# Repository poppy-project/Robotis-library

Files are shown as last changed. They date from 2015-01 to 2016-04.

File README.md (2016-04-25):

Robotis CAD library
===================

Solidworks library of Robotis CAD models.
It includes the Dynamixel AX-Series and MX/RX-series.

In addition, there are 3D printable parts allowing for compact double rotation assemblies (available for 3 configuration (MX64-MX64, MX64-MX28, MX28-MX28))
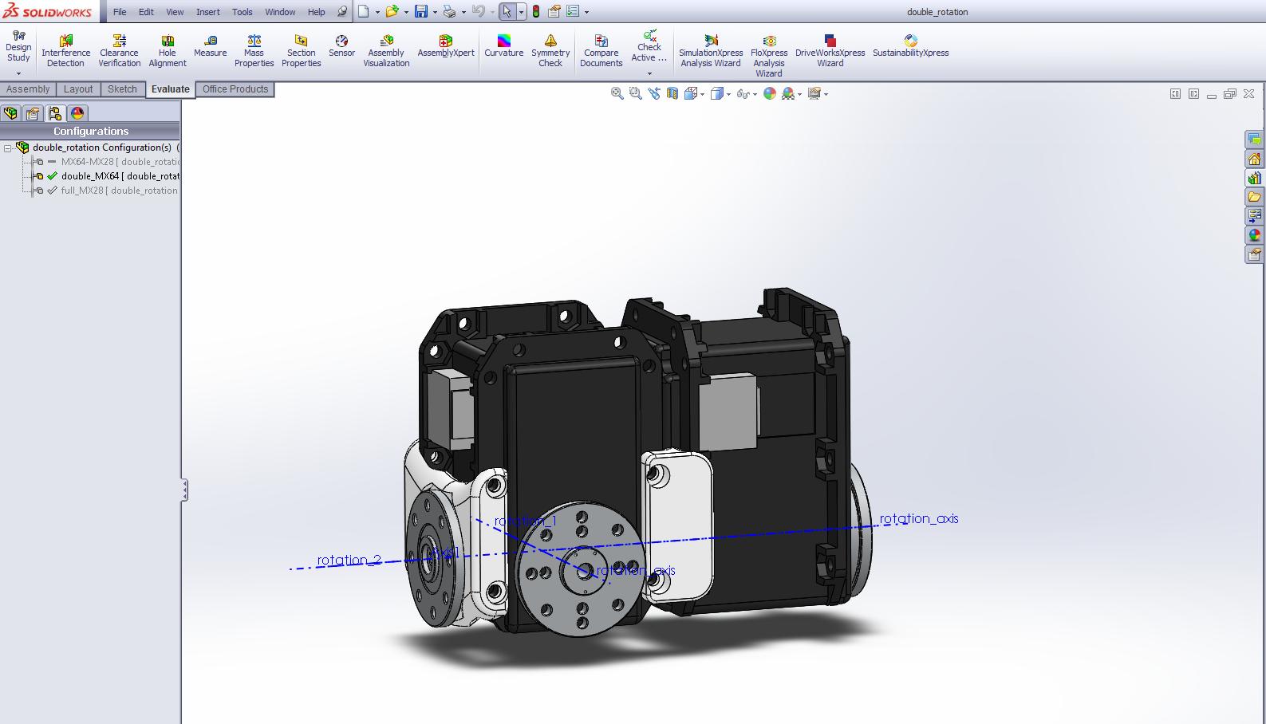
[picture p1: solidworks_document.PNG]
double-rotation


 **This work is licensed under a [Creative Commons Attribution-ShareAlike 4.0 International License](http://creativecommons.org/licenses/by-sa/4.0/).**

Please keep references to the Poppy project (www.poppy-project.org) and authors when you use or fork this work.

**Authors:** Matthieu Lapeyre, Alexandre Le Falher.

## Support

You need support ?
The [Poppy forum](https://forum.poppy-project.org/) is the best (and single) place to ask for help!

## Contribute

### /!\ SolidWorks version
The SolidWorks policy sucks, they intentionnaly break compatibility between recent and older version. If you have a Solidworks older than 2013-SP0 you will certainly be able to open these parts but only as a read-only mode, which is equivalent to not beign able to open it...

Therefore, we won't upgrade our SolidWorks so more people can easily modify parts for their own uses.

For the same reason, we ask potential contributors wanting to pull work into official repository to downgrade (if needed) their solidworks version to 2013.

Accepting a pull-request from a Soldiworks >= 2014 will break whole compatibility.

## The Poppy project history

The Poppy project is born in 2012 in the [Flowers laboratory](flowers.inria.fr) at [Inria Bordeaux Sud-Ouest](http://www.inria.fr/en/centre/bordeaux).
It was initiated during [Matthieu Lapeyre](github.com/matthieu-lapeyre)'s PhD Thesis surpervised by [Pierre Yves Oudeyer](http://www.pyoudeyer.com/). At the beginning, the development team was composed by Matthieu Lapeyre (mechanics & design), [Pierre Rouanet](github.com/pierre-rouanet) (software) and [Jonathan Grizou](http://jgrizou.com/) (electronics).

This project is initially a fundamental research project financed by [ERC Grant Explorer](http://erc.europa.eu/) to explore the role of embodiement and morphology properties on cognition and especially on the learning of sensori-motor tasks.

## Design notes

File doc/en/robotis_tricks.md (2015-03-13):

# /!\ Robotis Dynamixel Noobs Traps

When you want to assemble a Poppy, the first thing to do is to ensure yourself **you assembled correctly the horn on the Dynamixel motors**. This is both the first step and maybe the most critical one. An error in the configuration or assembly here is really boring to change once a Poppy creature is assembled.

## 1. Fix the horn on the motor
**Warning! This step is critical!**

Dynamixel motors are sold unassembled, you have to add manually the horn HN07-N101 (for MX-28) and HN05-N102 (for MX-64).
The critical aspect is to put the horn correctly on the zero position. To do that, you have to correctly align the awl mark on the Dynamixel shaft and the snick on the horn:

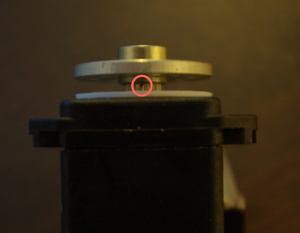
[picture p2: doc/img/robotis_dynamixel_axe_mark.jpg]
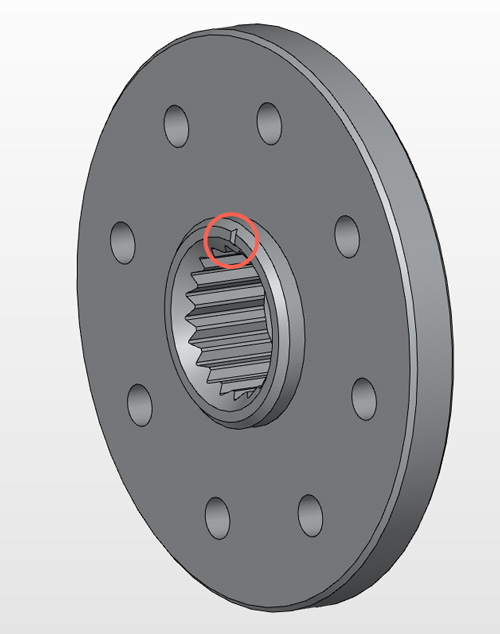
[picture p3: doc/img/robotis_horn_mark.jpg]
 

When assembled, the horn is really difficult to remove and you will probably damage the motor, so check twice or thrice !

Also, it is pretty hard to push the horn on the shaft, you will probably have to use the screw (M2.5x8mm) and tighten it to correctly assemble the two elements.

## 2. Motor configuration
When you take out the motor out of its box, its internal id is 1. So before plug it on the communication bus you have to configure it. Otherwise you will have problems such as experimented in this [topic](https://forum.poppy-project.org/t/dynamixel-first-uses/91/5).

You have 3 parameters to tune:

 1. the **id must match our [convention][1]**
 2. the **baudrate** have to be **set to 1 000 000bps** instead of 57142bps
 3. the **return delay time** have to be set to **0 ms** instead of 0.5 ms

To tune these parameters you can either use the [Dynamixel Wizard][2] (windows) or [Herborist][3] (Unix/Windows).
<a class="attachment" href="http://www.robotis.com/xe/download_en/657775">RoboPlus v1.1.1.0 </a>

If you are using [USB2AX dongles][4] under windows, you will need to install it manually using the <a class="attachment" href="https://github.com/Xevel/usb2ax/raw/master/firmware/lufa_usb2ax/USB2AX.inf">USB2AX.inf</a> (2 KB) file.
For more info about the installation procedure, please consult the [QuickStart guide][5].

  [1]: https://forum.poppy-project.org/t/assembly-instructions-motor-naming-convention-and-configuration/87
  [2]: http://support.robotis.com/en/software/roboplus/dynamixel_monitor/quickstart/dynamixel_monitor_connection.htm
  [3]: http://poppy-project.github.io/pypot/herborist.html
  [4]: http://www.xevelabs.com/doku.php?id=product:usb2ax:usb2ax
  [5]: http://www.xevelabs.com/doku.php?id=product:usb2ax:quickstart

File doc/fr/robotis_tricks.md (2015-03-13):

# /!\ Robotis Dynamixel : piège pour les débutants

Lorsque vous souhaitez assembler un Poppy, la première chose dont il faut vous assurer **est que vous assemblez correctement le palonnier des moteurs Dynamixel**. C'est à la fois la première étape et peut-être la plus critique. Une erreur dans la configuration ou l'assemblage de cette étape sera véritablement difficle à changer une fois que Poppy sera assemblé.

## 1. Gérer le palonnier sur le moteur
**ATTENTION ! Cette étape est critique !**

Les moteurs Dynamixel sont vendu non assemblés, vous aurez à ajouter manuellement le palonnier HN07-N101 (pour le modèle MX-28) et HN05-N102 (pour le modèle MX-64).
Le point critique est de placer le palonnier correctement, sur la position zéro. Pour le faire, vous aurez à aligner correctement la marque de poinçon de l'arbre avec l'entaille de le palonnier :

 

Quand montée, le palonnier est véritablement difficile à enlever et vous aurez certainement à endommager le moteur aussi, tourner sept fois vos doigts dans vos mains avant d'agir !

De même, il est assez difficile de placer le palonnier dans l'arbre, vous aurez certainement à utiliser une vis (M2.5x8mm) et la serrer pour assembler correctement les deux éléments.

## 2. Configuration des moteurs
Lorsque vous sortez le moteur de sa boîte, son ID interne est 1. Aussi, avant de le brancher sur le bus de communication, vous aurez à le configurer. Autrement vous aurez des problèmes comme expérimentés dans ce  [topic](https://forum.poppy-project.org/t/dynamixel-first-uses/91/5).

VOus avez trois paramètres à régler :

 1. L'**ID doit correspondre à notre [convention][1]**
 2. La **vitesse de transmission** doit être **réglée sur 1 000 000bps** au lieu de 57142bps
 3. Le  **délai de temps de retour** doit être réglé sur **0 ms** au lieu de 0.5 ms

Pour régler ces paramètres vous pouvez utiliser le [Dynamixel Wizard][2] (windows) ou [Herborist][3] (Unix/Windows).
<a class="attachment" href="http://www.robotis.com/xe/download_en/657775">RoboPlus v1.1.1.0 </a>

Si vous utilisez [une prise USB2AX][4] sous windows, vous aurez à l'installer manuellement en utilisant ce fichier : <a class="attachment" href="https://github.com/Xevel/usb2ax/raw/master/firmware/lufa_usb2ax/USB2AX.inf">USB2AX.inf</a> (2 KB).
Pour plus d'infos sur cette installation, merci de consulter le [guide d'installation][5].

  [1]: https://forum.poppy-project.org/t/assembly-instructions-motor-naming-convention-and-configuration/87
  [2]: http://support.robotis.com/en/software/roboplus/dynamixel_monitor/quickstart/dynamixel_monitor_connection.htm
  [3]: http://poppy-project.github.io/pypot/herborist.html
  [4]: http://www.xevelabs.com/doku.php?id=product:usb2ax:usb2ax
  [5]: http://www.xevelabs.com/doku.php?id=product:usb2ax:quickstart

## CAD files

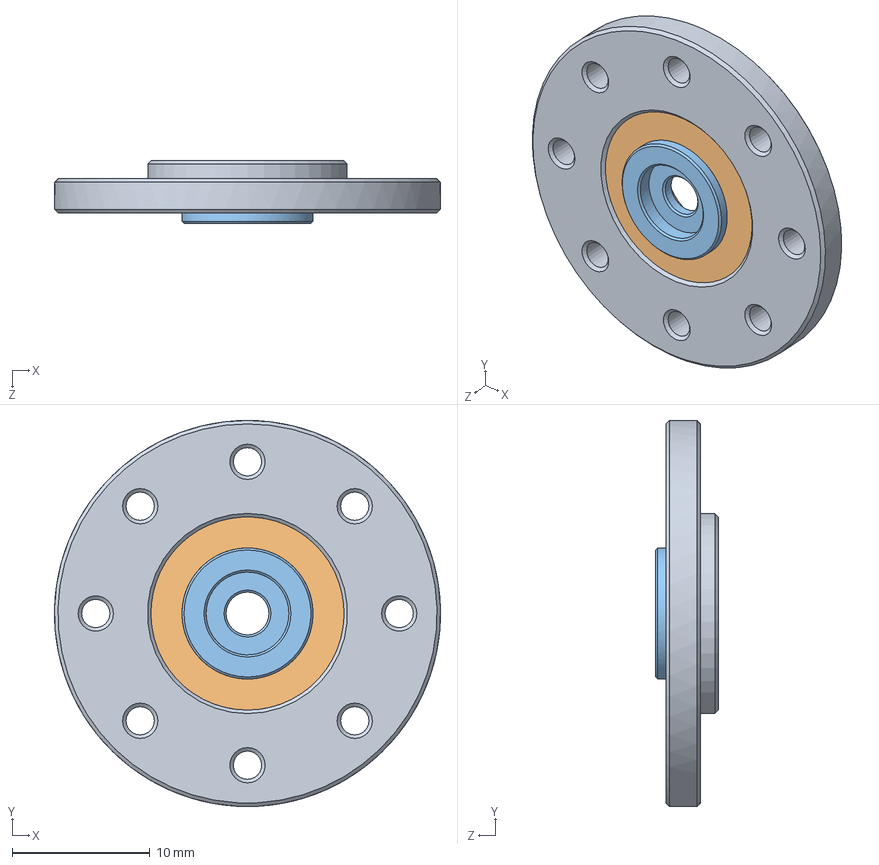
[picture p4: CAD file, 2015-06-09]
bearing/i101_Set.SLDASM
28.0 x 28.0 x 4.56 mm
HN05-i101
MF128ZZ
RX64-CAP

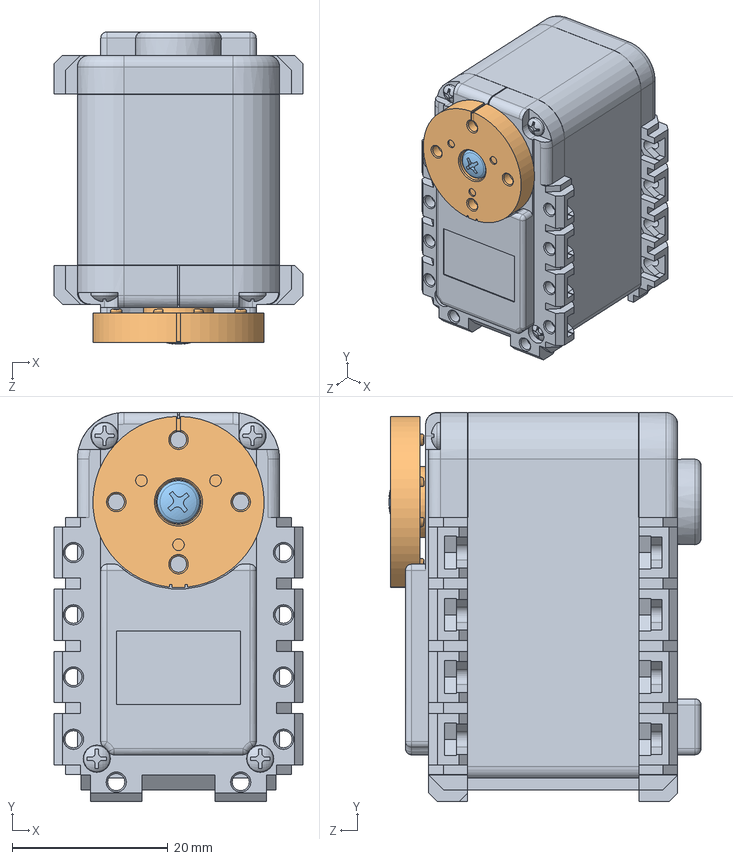
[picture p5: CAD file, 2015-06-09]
AX-12_18A.SLDASM
32.0 x 50.0 x 40.1 mm
dynamixel_AXseries
AX12_horn
BHS_M2_6X8

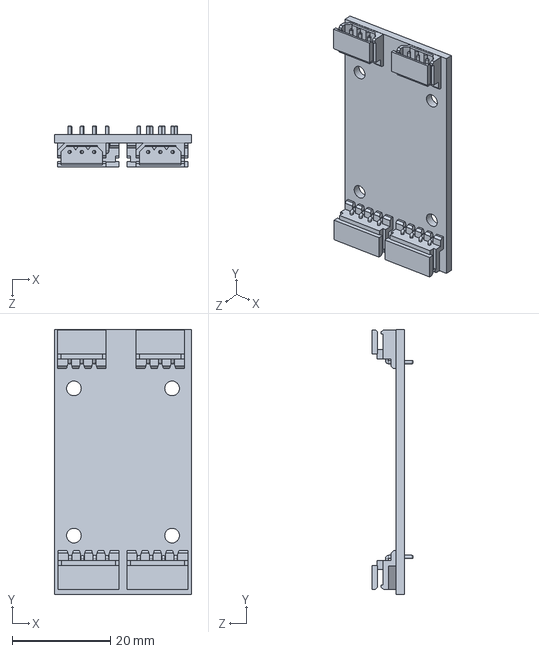
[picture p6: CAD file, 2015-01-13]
electronics/SMPS2Dynamixel.SLDPRT
28.0 x 54.0 x 8.40 mm

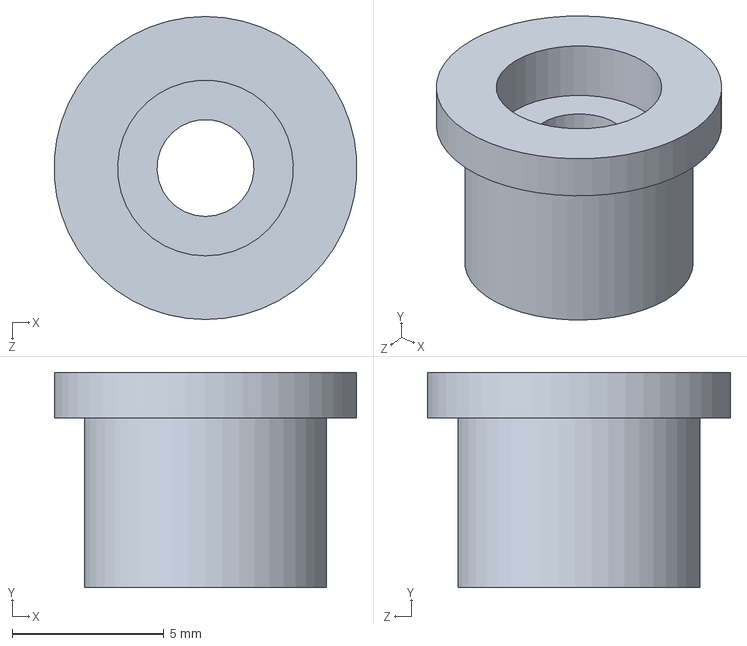
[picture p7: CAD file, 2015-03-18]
bearing/BPF-BU.SLDPRT
9.98 x 7.10 x 10.0 mm

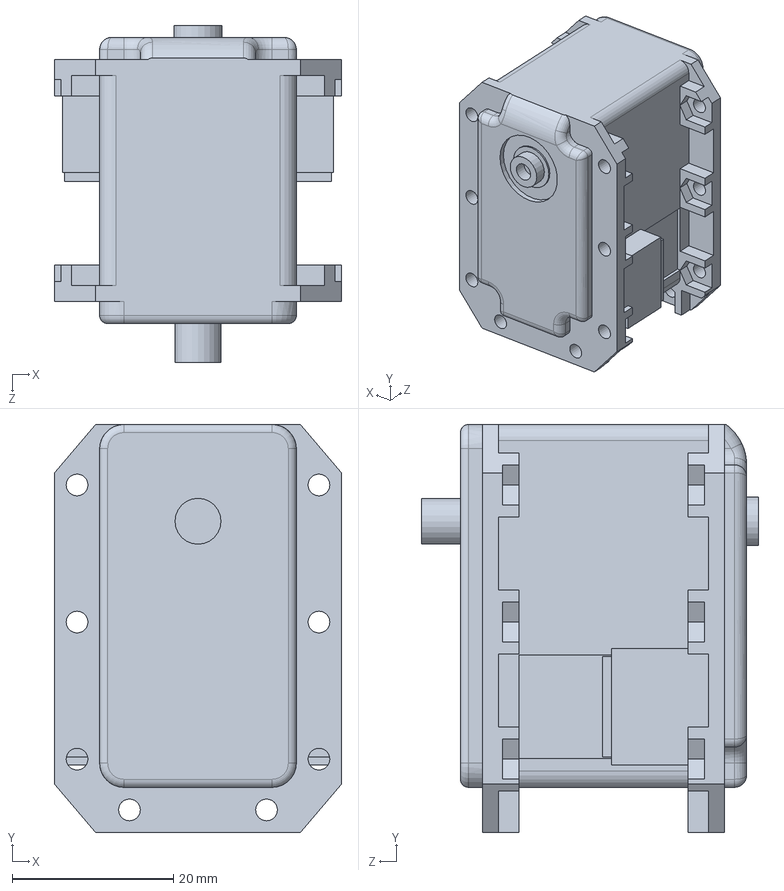
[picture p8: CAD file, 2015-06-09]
dynamixel/dynamixel_x28series.SLDPRT
35.6 x 50.6 x 41.9 mm

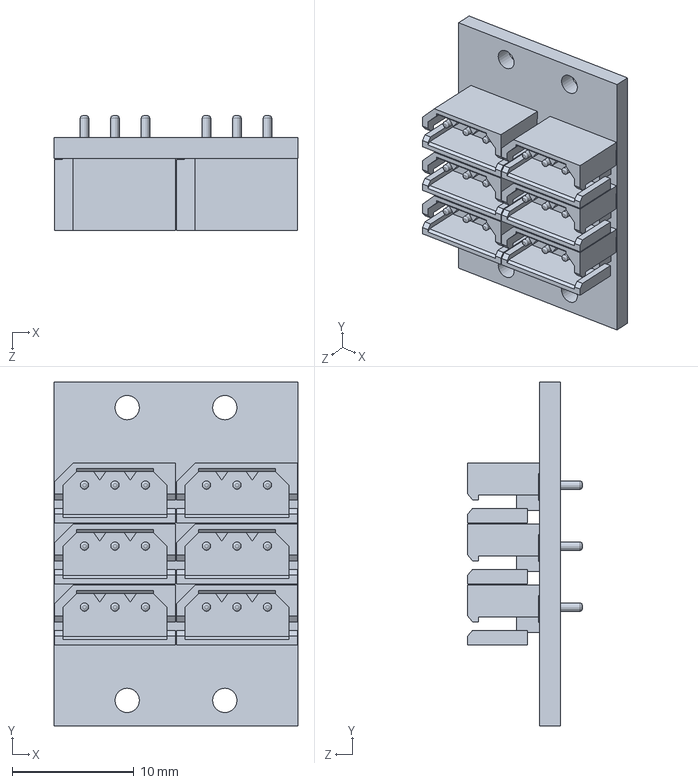
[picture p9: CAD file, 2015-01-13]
electronics/BIOLOID_3P_Extension_PCB.SLDPRT
20.0 x 28.2 x 9.40 mm

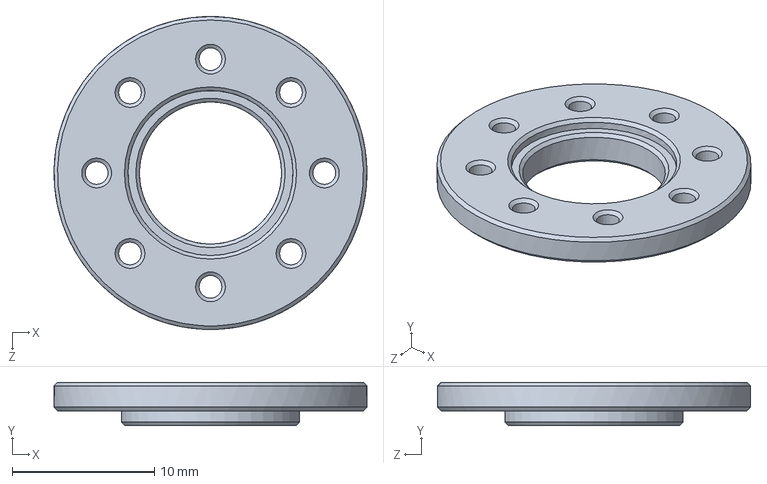
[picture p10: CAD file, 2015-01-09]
horn/HN07-i101.SLDPRT
22.0 x 3.05 x 22.0 mm

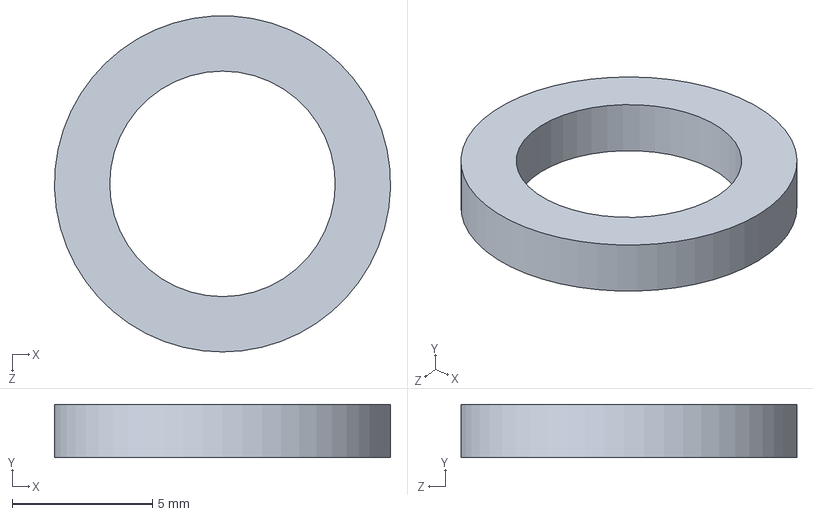
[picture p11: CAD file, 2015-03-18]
bearing/BPF-WA.SLDPRT
12.0 x 1.90 x 12.0 mm

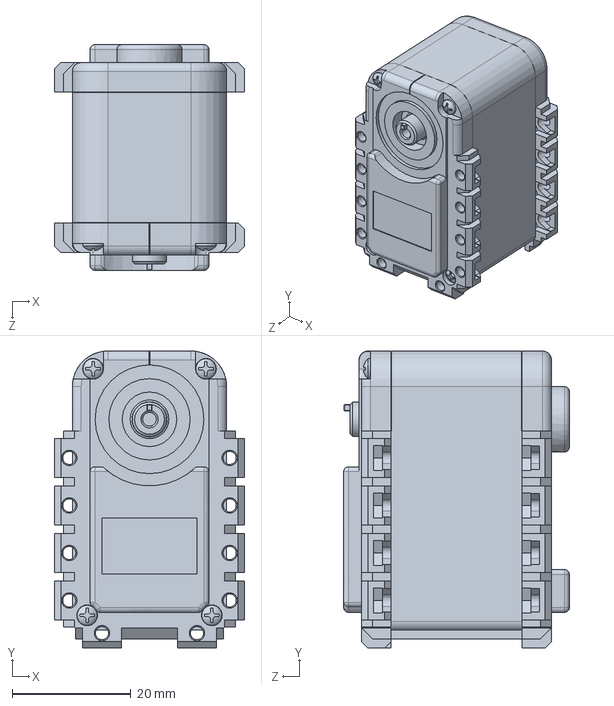
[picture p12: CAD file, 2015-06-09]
dynamixel/dynamixel_AXseries.SLDPRT
32.0 x 50.0 x 38.0 mm

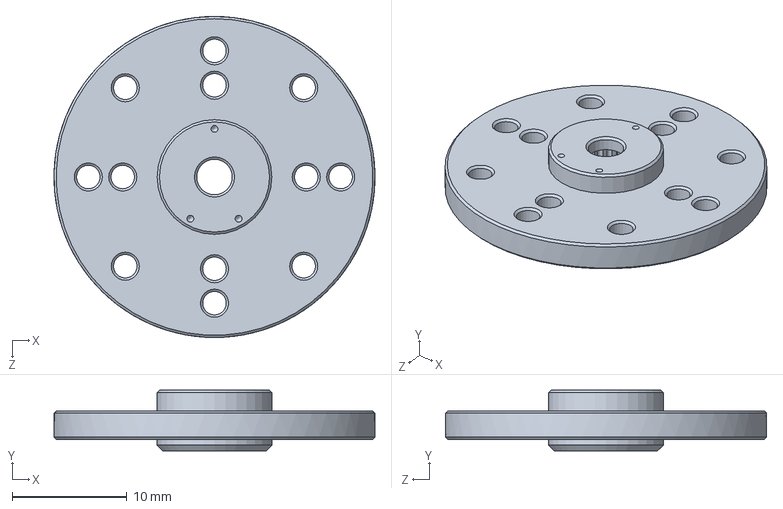
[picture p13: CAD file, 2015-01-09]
horn/HN05-N101.SLDPRT
28.0 x 5.30 x 28.0 mm

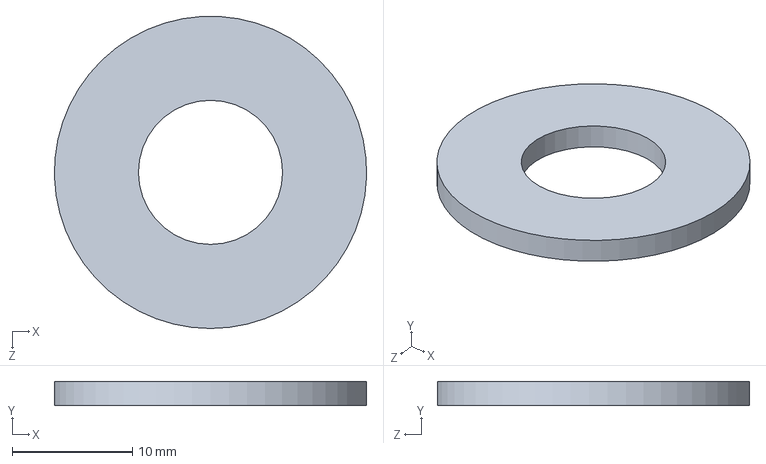
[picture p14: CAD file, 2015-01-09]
bearing/1226T.SLDPRT
26.0 x 2.00 x 26.0 mm

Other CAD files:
MX-106.SLDASM
MX-28.SLDASM
MX-64.SLDASM
double_rotation.SLDASM
dynamixel/dynamixel_x106series.SLDPRT
poppy_parts/double_rotation_link.SLDPRT
poppy_parts/i101-Set_to_MX_link.SLDPRT
bearing/AS1226.SLDPRT
bearing/MF106ZZ.SLDPRT
bearing/MF128ZZ.SLDPRT
bearing/RX28-CAP.SLDPRT
bearing/RX64-CAP.SLDPRT
bolt/BHS_M2_6X8.sldprt
bolt/WB_M2.5x8.SLDPRT
dynamixel/dynamixel_x64series.SLDPRT
horn/AX12_horn.SLDPRT
horn/HN05-T101.SLDPRT
horn/HN05-i101.SLDPRT
horn/HN07-N101.SLDPRT
horn/trust_washer.SLDPRT

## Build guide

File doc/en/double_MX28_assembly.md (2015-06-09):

# Double Dynamixel MX-28 AT/R assembly

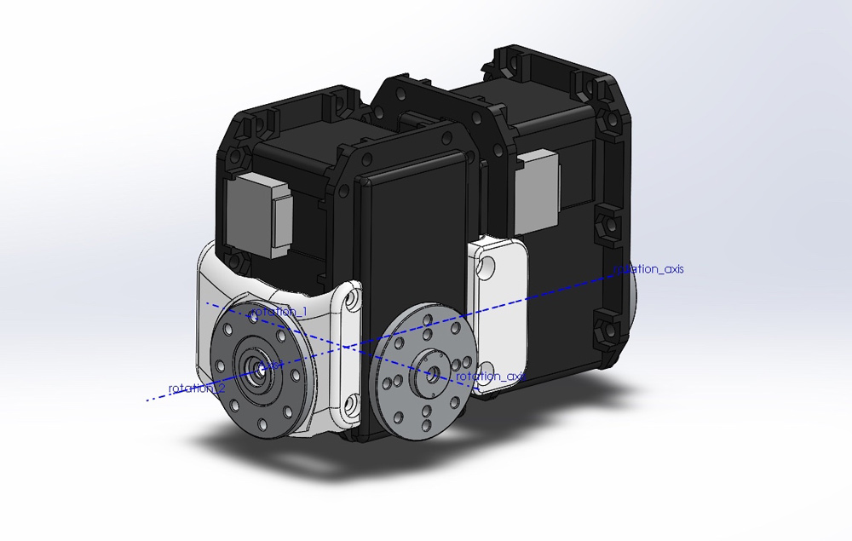
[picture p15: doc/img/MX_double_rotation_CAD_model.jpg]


- Preparation: 5-10 min
- Assembly: 20-25 min

## Requirement:
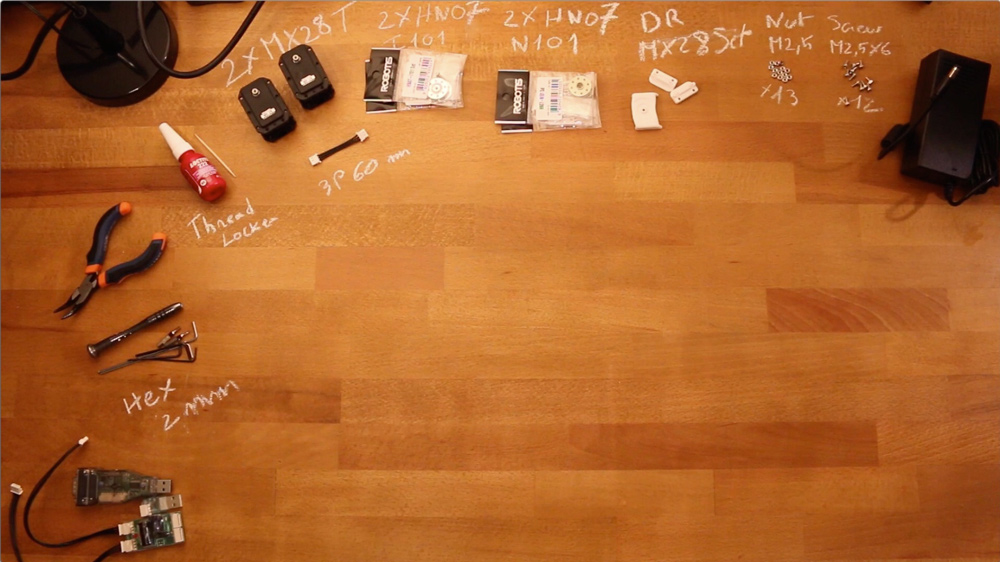
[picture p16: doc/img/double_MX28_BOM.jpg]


**3D Printed parts**:
- 1x i101-Set_to_MX28_link
- 2x double_rotation_MX28_link

**Actuators:**
- 2x Robotis Dynamixel MX28-AT

**Cables**:
- 1x 3P 60mm

**Robotis parts:**
- 2x HN07-N101
- 2x HN07-I101
- 13x Nuts M2.5
- 12x Bolts M2.5x6
- 1x Bolts M2.5x8

**Motor configuration:**
- 1x Alimentation 12V
- 1x SMPS2Dynamixel
- 1x USB2Dynamixel or USB2AX
- A computer...

## Assembly instructions:

- **Step 1:** Ensure you have read [**this note**](robotis_tricks.md) before continuing to avoid the classic (and critical) traps when using Robotis Dynamixel actuators.
- **Step 2**: Click on the image below to display the video:
Double MX28 Assembly (http://youtu.be/9oNGV9ggHaE)

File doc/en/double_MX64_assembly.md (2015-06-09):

# Double Dynamixel MX-64 AT/R assembly

Chest Assembly

- Preparation: 105 min
- Assembly: 20-25 min

## Requirement:
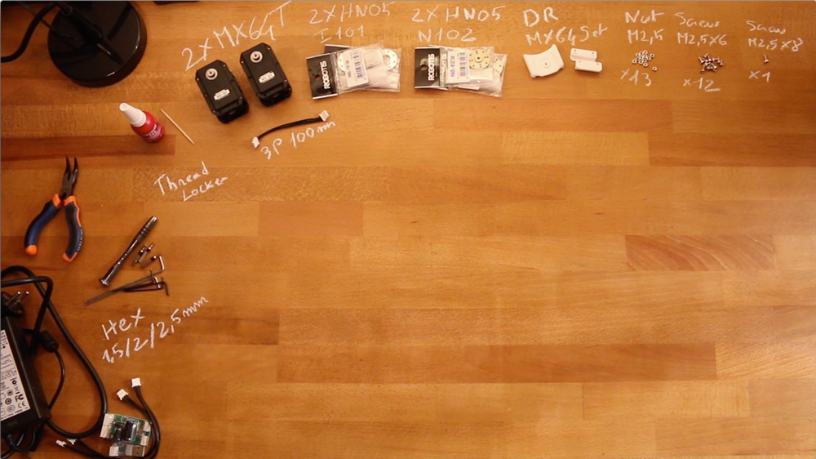
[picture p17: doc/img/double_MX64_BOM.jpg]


**3D Printed parts**:
- 1x i101-Set_to_MX64_link
- 2x double_rotation_MX64_link

**Actuators:**
- 2x Robotis Dynamixel MX64-AT

**Cables**:
- 1x 3P 100mm

**Robotis parts:**
- 2x HN05-N102
- 2x HN05-I101
- 13x Nuts M2.5
- 12x Bolts M2.5x6
- 1x Bolts M2.5x8

**Motor configuration:**
- 1x Alimentation 12V
- 1x SMPS2Dynamixel
- 1x USB2Dynamixel or USB2AX
- A computer...

## Assembly instructions:

- **Step 1:** Ensure you have read [**this note**](robotis_tricks.md) before continuing to avoid the classic (and critical) traps when using Robotis Dynamixel actuators.
- **Step 2**: Click on the image below to display the video:
Double MX64 Assembly (http://youtu.be/83lrhXVNHYE)

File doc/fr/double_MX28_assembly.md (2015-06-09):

# Assemblage des Double Dynamixel MX-28 AT/R

Assemblage de la poitrine

- Préparation: 5-10 min
- Assemblage : 20-25 min

## Exigences :
Assemblage de la poitrine

**Partie imprimées en 3D**:
- 1x i101-Set_to_MX28_link
- 2x double_rotation_MX28_link

**Actionneurs :**
- 2x Robotis Dynamixel MX28-AT

**Câbles**:
- 1x 3P 60mm

**Parties Robotis :**
- 2x HN07-N101
- 2x HN07-I101
- 13x écrous M2.5
- 12x vis M2.5x6
- 1x vis M2.5x8

**COnfiguration des moteurs :**
- 1x Alimentation 12V
- 1x SMPS2Dynamixel
- 1x USB2Dynamixel or USB2AX
- Un ordinateur...

## Instructions d'assemblage :

- **Etape 1:** Assurez-vous d'avoir lu [**cette note**](robotis_tricks.md) avant de continuer pour éviter les pièges classiques (et critiques) rencontrés lors de l'utilisation des actionneurs Robotis Dynamixel.
- **Etape 2**: CLiquez sur l'image ci-dessous pour afficher la vidéo :
Assemblage du Double MX28 (http://youtu.be/9oNGV9ggHaE)

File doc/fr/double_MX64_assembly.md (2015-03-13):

# Assemblage des MX-64 AT/R Double Dynamixel

Assemblage de la poitrine

- Préparation: 105 min
- Assemblage : 20-25 min

## Exigences :
Assemblage de la poitrine

**Parties imprimées en 3D **:
- 1x i101-Set_to_MX64_link
- 2x double_rotation_MX64_link

**Actionneurs :**
- 2x Robotis Dynamixel MX64-AT

**Câbles **:
- 1x 3P 100mm

**Parties Robotis :**
- 2x HN05-N102
- 2x HN05-I101
- 13x écrous M2.5
- 12x vis M2.5x6
- 1x vis M2.5x8

**Motor configuration:**
- 1x Alimentation 12V
- 1x SMPS2Dynamixel
- 1x USB2Dynamixel or USB2AX
- Un ordinateur...

## Instruction d'assemblage :

- **Etape 1:** Assurez-vous d'avoir lu [**cette note**](robotis_tricks.md) avant de continuer pour éviter les pièges classiques (et critiques) dans l'utilisation des actionneurs Robotis Dynamixel.
- **Etape 2**: Cliquez sur l'image ci-dessous pour afficher la vidéo :
Assemblage des Double MX64 (http://youtu.be/83lrhXVNHYE)

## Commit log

2015-01-09 Add Robotis horn and bearing parts
    [1226T.SLDPRT, AS1226.SLDPRT, AX12_horn.SLDPRT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]
2015-01-13 add Robotis Dynamixel motors
    [dynamixel_AXseries.SLDPRT, dynamixel_x106series.SLDPRT, dynamixel_x28series.SLDPRT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]
2015-01-13 add Dynamixel motor assemblies
    [AX-12_18A.SLDASM, BHS_M2_6X8.sldprt, MX-28.SLDASM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]
2015-01-13 add Robotis electronics components
    [BIOLOID_3P_Extension_PCB.SLDPRT, SMPS2Dynamixel.SLDPRT]
2015-01-13 add double_rotation assembly with custom 3D printed parts
    [double_rotation.SLDASM, double_rotation_link.SLDPRT, i101-Set_to_MX_link.SLDPRT]
2015-02-15 Add assembly instructions for double rotation configurations (MX64 and MX28)
2015-02-19 update documentation to include stuffs about the Robotis Dynamixel assembly
2015-02-26 increase thickness under so horn to improve robustness
    [i101-Set_to_MX_link.SLDPRT]
2015-03-18 Add BPF-BU and BPF-WA
    [BPF-BU.SLDPRT, BPF-WA.SLDPRT]
2015-04-09 update materials
    [AX-12_18A.SLDASM, MX-64.SLDASM, double_rotation.SLDASM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]
2016-05-02 update solidworks file for LFS
    [MX-28.SLDASM, MX-64.SLDASM, double_rotation.SLDASM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]
2016-09-08 add the MX-106 in the library
    [MX-106.SLDASM, dynamixel_x106series.SLDPRT]
